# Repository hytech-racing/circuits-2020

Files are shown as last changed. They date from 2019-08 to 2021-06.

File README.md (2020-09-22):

HyTech Logo

# 2020 Circuits

Repository for all of the circuits for the 2019-2020 car.

## Getting Started with this Git Repository
1. Follow HyTech's [Software Guide](https://github.com/hytech-racing/training/tree/master/Resources).
2. Create a GitHub account if you don't already have one.
3. Download and install [GitHub Desktop](https://desktop.github.com/) (basic) or [Git CLI](https://git-scm.com/book/en/v2/Getting-Started-Installing-Git) (advanced).
    * If you are using GitHub Desktop for the first time, be sure to read the [User Guide](https://help.github.com/desktop/guides/).
    * If you are using Git for the first time, you should start off by reading a tutorial. There are many available online:
        * [Pro Git book](https://git-scm.com/book/en/v2)
        * [Atlassian Git Tutorial](https://www.atlassian.com/git/tutorials/)
    * You may want to keep a copy of [GitHub's Git Cheat Sheet](https://services.github.com/kit/downloads/github-git-cheat-sheet.pdf) as a reference.
4. Talk to your subteam lead to be added to the team within the GitHub organization.
5. Clone this repository to your computer using the URLs:
    * SSH: `git@github.com:hytech-racing/circuits-2020.git`
    * HTTPS: `https://github.com/hytech-racing/circuits-2020.git`

## Getting Started with EAGLE
1. Follow HyTech's [Software Guide](https://github.com/hytech-racing/training/tree/master/Resources).
2. Download and install [EAGLE](https://www.autodesk.com/products/eagle/overview)
3. Get the free [Educational License](https://www.autodesk.com/education/free-software/eagle) (a .edu email address is required)

## Circuit Board Versioning Scheme
* New boards must start their numbering at revision 1.
* Revision numbers must be incremented by 1 when a physical board is manufactured, but not at any other time.
* After a board is manufactured, the files corresponding to the manufactured version should not be modified.
* Circuit boards based off of a previous year's design should increment based off of the previous board's revision number.

## More Information
* [Software Guide](https://github.com/hytech-racing/training/tree/master/Resources)
* [Team Site](https://hytechracing.gatech.edu/)
* [Facebook](https://www.facebook.com/HyTechRacing/)
* [Engage](https://gatech.campuslabs.com/engage/organization/hytech-racing)

## License
This project is licensed under the GPL License v3.0. See the [LICENSE](LICENSE) file for more information.

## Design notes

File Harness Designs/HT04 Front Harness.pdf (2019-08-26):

QA

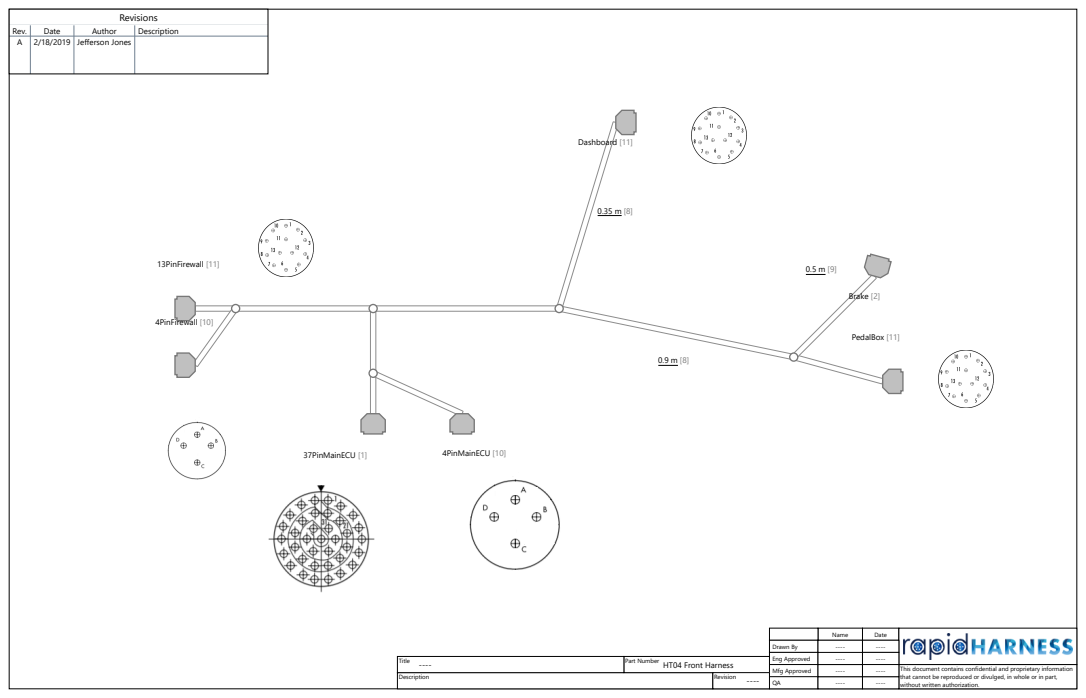
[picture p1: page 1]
Description; Mfg Approved; Part Number; Revision; Revisions; Brake [2]; Dashboard [11]; 4PinFirewall [10]; 13PinFirewall [11]; 37PinMainECU [1] 4PinMainECU [10]; PedalBox [11]

Rev. Date Author Description
A 2/18/2019 Jefferson Jones
Title HT04 Front Harness

Name Date
Drawn By
Eng Approved
This document contains confidential and proprietary information
that cannot be reproduced or divulged, in whole or in part,
without written authorization.

Id Type Manufacturer Part Number Description Quantity Usage

### 1 Connector TE:Deutsch AS614-35PN 37 Pin Plug, 22 Gauge 1 37PinMainECU

### 2 Connector 3 Cavity Generic Connector 1 Brake

3 Wire 22 AWG Red Generic Wire ≥ 3.55 m ACCEL1_5V, ACCEL2_5V,
BRAKE_5V, BrakeLight,
DASH12V, InverterSupply, SSOK
4 Wire 22 AWG White Generic Wire ≥ 4.2 m DASH1, DASH2, DASH3, DASH4,
DASH5, DASH6, DASH7, DASH8, DASH9, DASH10, DASH11, DASH12
5 Wire 22 AWG Green Generic Wire ≥ 3.2 m ACCEL1_GND, ACCEL2_GND,
BRAKE_GND
6 Wire 22 AWG Yellow Generic Wire ≥ 3.2 m ACCEL1, ACCEL2, BMSOK, BRAKE,
LatchEXTButton, OKHS, W4, W5
7 Wire 16 AWG Violet Generic Wire ≥ 2.5 m SHUTDOWN_D, SHUTDOWN_E,
SHUTDOWN_F, W1

### 8 Tubing Raychem 1/2" Raychem 1/2" 1.25 m See Drawing

### 9 Tubing Raychem 1/4" Raychem 1/4" 0.5 m See Drawing

### 10 Connector TE:Deutsch AS612-04SN 4 Pin Plug, 16 Gauge 2 4PinFirewall, 4PinMainECU

11 Connector TE:Deutsch AS610-35PN Plug 13 Pin Autosport Connector 3 13PinFirewall, Dashboard,
PedalBox

### 12 Wire 16 AWG Green Generic Wire Fan1GND, GND, PumpGND

### 13 Wire 16 AWG Red Generic Wire 12VIN, Fan1

### 14 Cable CAN Cable Cable for CAN Communications and Power CBL1

### 15 Wire 22 AWG Black Generic Wire ≥ 0.35 m DASHGND, GNDShield

### Bill of Materials 1 of 1 Page 2 of 6

Part Number:

Title:

Description:

HT04 Front Harness

### From To Conductor Conductor PN Twisted With Gauge Length From Contact PN Notes

4PinFirewall.1 4PinMainECU.1 12VIN.Red 16 AWG Red 16 AWG
4PinFirewall.2 4PinMainECU.2 PumpGND.Green 16 AWG Green 16 AWG
4PinFirewall.3 4PinMainECU.3 Fan1GND.Green 16 AWG Green 16 AWG
4PinFirewall.4 4PinMainECU.4 GND.Green 16 AWG Green 16 AWG 13PinFirewall.12 Dashboard.13 SHUTDOWN_F.Violet 16 AWG Violet 16 AWG ≥ 0.35 m 13PinFirewall.13 Dashboard.16 SSOK.Red 22 AWG Red 22 AWG ≥ 0.35 m 37PinMainECU.1 Dashboard.2 DASH1.White 22 AWG White 22 AWG ≥ 0.35 m 37PinMainECU.2 Dashboard.3 DASH2.White 22 AWG White 22 AWG ≥ 0.35 m 37PinMainECU.3 Dashboard.4 DASH3.White 22 AWG White 22 AWG ≥ 0.35 m 37PinMainECU.4 Dashboard.5 DASH4.White 22 AWG White 22 AWG ≥ 0.35 m 37PinMainECU.5 PedalBox.12 SHUTDOWN_D.Violet 16 AWG Violet 16 AWG ≥ 0.9 m 37PinMainECU.6 Dashboard.12 DASH11.White 22 AWG White 22 AWG ≥ 0.35 m 37PinMainECU.7 13PinFirewall.2 InverterSupply.Red 22 AWG Red 22 AWG 37PinMainECU.8 Brake.3 BRAKE.Yellow 22 AWG Yellow 22 AWG ≥ 1.4 m 37PinMainECU.9 13PinFirewall.3 BrakeLight.Red 22 AWG Red 22 AWG 37PinMainECU.10 13PinFirewall.4 CBL1.Red-PWR CAN Cable 22 AWG 37PinMainECU.11 13PinFirewall.5 CBL1.White-CANL CAN Cable 22 AWG 37PinMainECU.12 13PinFirewall.6 CBL1.Green-CANH CAN Cable 22 AWG 37PinMainECU.14 Brake.2 BRAKE_GND.Green 22 AWG Green 22 AWG ≥ 1.4 m 37PinMainECU.15 PedalBox.1 ACCEL2_GND.Green 22 AWG Green 22 AWG ≥ 0.9 m 37PinMainECU.16 PedalBox.5 ACCEL1_GND.Green 22 AWG Green 22 AWG ≥ 0.9 m 37PinMainECU.17 13PinFirewall.7 Fan1.Red 16 AWG Red 16 AWG 37PinMainECU.18 Dashboard.6 DASH5.White 22 AWG White 22 AWG ≥ 0.35 m 37PinMainECU.19 Dashboard.7 DASH6.White 22 AWG White 22 AWG ≥ 0.35 m 37PinMainECU.20 Dashboard.8 DASH7.White 22 AWG White 22 AWG ≥ 0.35 m 37PinMainECU.21 Dashboard.9 DASH8.White 22 AWG White 22 AWG ≥ 0.35 m 37PinMainECU.22 Dashboard.13 DASH12.White 22 AWG White 22 AWG ≥ 0.35 m 37PinMainECU.23 Dashboard.10 DASH9.White 22 AWG White 22 AWG ≥ 0.35 m 37PinMainECU.24 PedalBox.4 ACCEL2.Yellow 22 AWG Yellow 22 AWG ≥ 0.9 m 37PinMainECU.25 PedalBox.3 ACCEL1.Yellow 22 AWG Yellow 22 AWG ≥ 0.9 m 37PinMainECU.27 PedalBox.6 ACCEL1_5V.Red 22 AWG Red 22 AWG ≥ 0.9 m 37PinMainECU.28 PedalBox.2 ACCEL2_5V.Red 22 AWG Red 22 AWG ≥ 0.9 m 37PinMainECU.29 Brake.1 BRAKE_5V.Red 22 AWG Red 22 AWG ≥ 1.4 m 37PinMainECU.30 13PinFirewall.8 CBL1.Black-GND CAN Cable 22 AWG 37PinMainECU.31 13PinFirewall.9 BMSOK.Yellow 22 AWG Yellow 22 AWG 37PinMainECU.32 Dashboard.11 DASH10.White 22 AWG White 22 AWG ≥ 0.35 m 37PinMainECU.33 13PinFirewall.10 OKHS.Yellow 22 AWG Yellow 22 AWG 37PinMainECU.36 13PinFirewall.1 GNDShield.Black 22 AWG Black 22 AWG 37PinMainECU.36 Dashboard.1 DASHGND.Black 22 AWG Black 22 AWG ≥ 0.35 m
37PinMainECU.37 13PinFirewall.11 LatchEXTButton.Yellow 22 AWG Yellow 22 AWG
Dashboard.12 PedalBox.13 SHUTDOWN_E.Violet 16 AWG Violet 16 AWG ≥ 1.25 m

### Wiring Table 1 of 1 Page 3 of 6

Description:

### # Type Reference Designator Manufacturer Part Number Color Gauge Length Twisted With

### 1 Cable CBL1 CAN Cable Gray

### 2 Wire 12VIN 16 AWG Red Red 16 AWG

### 3 Wire ACCEL1 22 AWG Yellow Yellow 22 AWG ≥ 0.9 m 4 Wire ACCEL1_5V 22 AWG Red Red 22 AWG ≥ 0.9 m

### 5 Wire ACCEL1_GND 22 AWG Green Green 22 AWG ≥ 0.9 m

### 6 Wire ACCEL2 22 AWG Yellow Yellow 22 AWG ≥ 0.9 m 7 Wire ACCEL2_5V 22 AWG Red Red 22 AWG ≥ 0.9 m

### 8 Wire ACCEL2_GND 22 AWG Green Green 22 AWG ≥ 0.9 m

### 9 Wire BMSOK 22 AWG Yellow Yellow 22 AWG

### 10 Wire BRAKE 22 AWG Yellow Yellow 22 AWG ≥ 1.4 m 11 Wire BRAKE_5V 22 AWG Red Red 22 AWG ≥ 1.4 m

### 12 Wire BRAKE_GND 22 AWG Green Green 22 AWG ≥ 1.4 m

### 13 Wire BrakeLight 22 AWG Red Red 22 AWG

14 Wire DASH1 22 AWG White White 22 AWG ≥ 0.35 m 15 Wire DASH2 22 AWG White White 22 AWG ≥ 0.35 m 16 Wire DASH3 22 AWG White White 22 AWG ≥ 0.35 m 17 Wire DASH4 22 AWG White White 22 AWG ≥ 0.35 m 18 Wire DASH5 22 AWG White White 22 AWG ≥ 0.35 m 19 Wire DASH6 22 AWG White White 22 AWG ≥ 0.35 m 20 Wire DASH7 22 AWG White White 22 AWG ≥ 0.35 m 21 Wire DASH8 22 AWG White White 22 AWG ≥ 0.35 m 22 Wire DASH9 22 AWG White White 22 AWG ≥ 0.35 m 23 Wire DASH10 22 AWG White White 22 AWG ≥ 0.35 m 24 Wire DASH11 22 AWG White White 22 AWG ≥ 0.35 m 25 Wire DASH12 22 AWG White White 22 AWG ≥ 0.35 m

### 26 Wire DASH12V 22 AWG Red Red 22 AWG 0 in

### 27 Wire DASHGND 22 AWG Black Black 22 AWG ≥ 0.35 m

### 28 Wire Fan1 16 AWG Red Red 16 AWG

### 29 Wire Fan1GND 16 AWG Green Green 16 AWG 30 Wire GND 16 AWG Green Green 16 AWG

### 31 Wire GNDShield 22 AWG Black Black 22 AWG

### 32 Wire InverterSupply 22 AWG Red Red 22 AWG

### 33 Wire LatchEXTButton 22 AWG Yellow Yellow 22 AWG 34 Wire OKHS 22 AWG Yellow Yellow 22 AWG

### 35 Wire PumpGND 16 AWG Green Green 16 AWG

### 36 Wire SHUTDOWN_D 16 AWG Violet Violet 16 AWG ≥ 0.9 m

### 37 Wire SHUTDOWN_E 16 AWG Violet Violet 16 AWG ≥ 1.25 m 38 Wire SHUTDOWN_F 16 AWG Violet Violet 16 AWG ≥ 0.35 m

### 39 Wire SSOK 22 AWG Red Red 22 AWG ≥ 0.35 m

### 40 Wire W1 16 AWG Violet Violet 16 AWG 0 in 41 Wire W4 22 AWG Yellow Yellow 22 AWG 0 in

### Cutlist 1 of 2 Page 4 of 6

Description:

### # Type Reference Designator Manufacturer Part Number Color Gauge Length Twisted With

### 42 Wire W5 22 AWG Yellow Yellow 22 AWG 0 in

### Cutlist 2 of 2 Page 5 of 6

Description:

# Manufacturer Part Number Description Label Text

### Labels 1 of 1 Page 6 of 6

Description:

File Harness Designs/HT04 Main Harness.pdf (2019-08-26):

QA

1

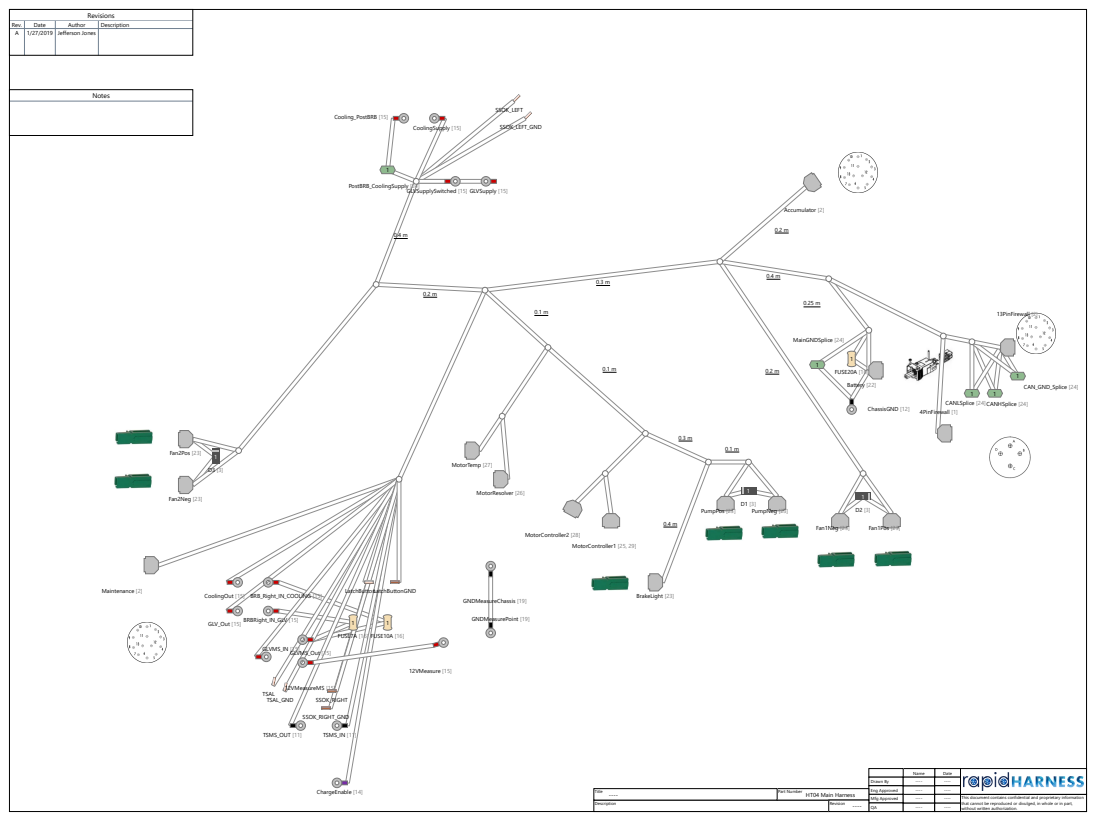
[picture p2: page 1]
Description; Mfg Approved; Part Number; Revision; Title HT04 Main Harness; Notes; Revisions; Accumulator [2]; Battery [22]; MotorController1 [25, 29]; Fan1Neg [23] Fan1Pos [23]; Fan2Pos [23] Fan2Neg [23]; PumpPos [23] PumpNeg [23]; BrakeLight [23]; 13PinFirewall [2]; 4PinFirewall [1]; Maintenance [2]; MotorResolver [26]; MotorTemp [27]; MotorController2 [28]; SSOK_RIGHT; TSAL; LatchButton; SSOK_LEFT; LatchButtonGND; TSAL_GND; SSOK_RIGHT_GND; SSOK_LEFT_GND; TSMS_IN [11]; ChassisGND [12]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

Rev. Date Author Description
A 1/27/2019 Jefferson Jones

Name Date
Drawn By
Eng Approved
This document contains confidential and proprietary information
that cannot be reproduced or divulged, in whole or in part,
without written authorization.

Id Type Manufacturer Part Number Description Quantity Usage

### 1 Connector TE:Deutsch AS612-04SN 4 Pin Plug, 16 Gauge 1 4PinFirewall

2 Connector TE AS610-35PN Plug 13 Pin Autosport Connector 3 13PinFirewall, Accumulator,
Maintenance

### 3 Diode Generic Diode Generic Diode 3 D1, D2, D3

4 Wire 16 AWG Red Generic Wire ≥ 8.65 m 12VBattery_toFuse,
12VMeasureCable,
12V_IntoMainECU,
BatteryFuse_toGLVMS,
CoolingPWR,
Cooling_RightBRB_toLeftBRB, Cooling_toRightBRB, Fan1PWR,
Fan2PWR,
GLV_RightBRB_toLeftBRB,
GLV_ToCoolingFuse,
GLV_ToECUFuse,
LVFused_toRightBRB, PumpPWR,
SSOKL, SSOKR, TSALPWR

### 5 Wire 16 AWG Brown Generic Wire 0 in W10, W11, W12, W13, W14, W15

6 Wire 22 AWG White Generic Wire ≥ 1.5 m DASH12,
MCMaintFaultIndication,
MCMaintRX, MCMaintTX,
MCMaintXDCR_PWR, MotorCosNeg,
MotorCosPos, MotorExcNeg,
MotorExcPos, MotorSinNeg,
MotorSinPos, MotorTempNeg
7 Wire 22 AWG Red Generic Wire ≥ 1.6 m BrakeLightPWR, BrakePWR,
DASH12V, PedalPWR1, PedalPWR2

### 8 Wire 22 AWG Brown Generic Wire 0 in W29, W30, W31

9 Wire 22 AWG Yellow Generic Wire ≥ 2.2 m BMSOK, BrakeSignal,
LatchButtonSignal,
MCMaintProgEnable,
MotorTempPos, OKHS
10 Wire 16 AWG Violet Generic Wire ≥ 1.7 m ChargeEnableSignal,
MaintChargeEnable,
SHUTDOWN_F, SHUTDOWN_G

### 11 Ring Terminal Unspecified gauge Black Generic Ring Terminal 2 TSMS_IN, TSMS_OUT

### 12 Ring Terminal 14-12 AWG Black Generic Ring Terminal 1 ChassisGND

13 Cable CAN Cable Cable for CAN Communications and Power ≥ 2.2 m AccumCAN, CANMaint,
MotorController_CAN

### 14 Ring Terminal Unspecified gauge Violet Generic Ring Terminal 1 ChargeEnable

15 Ring Terminal Unspecified gauge Red Generic Ring Terminal 12 12VMeasure, 12VMeasureMS,

### Bill of Materials 1 of 2 Page 2 of 9

Part Number:

Title:

Description:

HT04 Main Harness

Id Type Manufacturer Part Number Description Quantity Usage
BRBRight_IN_GLV,
BRB_Right_IN_COOLING,
CoolingOut, CoolingSupply, Cooling_PostBRB, GLVMS_IN,
GLVMS_Out, GLVSupply,
GLVSupplySwitched, GLV_Out

### 16 Resistor Generic Resistor Generic Resistor 3 FUSE7A, FUSE10A, FUSE20A

17 Wire 16 AWG Green Generic Wire ≥ 6.5 m Fan1GND, Fan2GND,
GLVBattery_ChassisGND,
GNDMeasure, MainECUGND,
PumpGND, SSOKL_GND,
SSOKR_GND, TSALGND, W65

### 18 Wire 22 AWG Black Generic Wire ≥ 0.2 m MCMaintGND

19 Ring Terminal 26-22 AWG Black Generic Ring Terminal 2 GNDMeasureChassis,
GNDMeasurePoint
20 Wire 22 AWG Green Generic Wire ≥ 2.8 m Accel1GND, Accel2GND,
BrakeGND,
BrakeLightGNDConnection,
LatchGND, W70

### 21 Wire 16 AWG Black Generic Wire MainGNDSpliceToGND

### 22 Connector ASMPP30-1X2-RK Anderson PowerPole 1X2 1 Battery

23 Connector 1327G6-BK Anderson PowerPole 1 7 BrakeLight, Fan1Neg, Fan1Pos,
Fan2Neg, Fan2Pos, PumpNeg,
PumpPos
24 Splice Generic Splice Generic Splice 5 CANHSplice, CANLSplice,
CAN_GND_Splice,
MainGNDSplice,
PostBRB_CoolingSupply

### 25 Boot TE 776463/776464 Ampseal Boot 1 MotorController1

### 26 Connector 8STA60835SN 1 MotorResolver

### 27 Connector 8STA60235SN 1 MotorTemp

### 28 Connector 8 Cavity Generic Connector 1 MotorController2

### 29 Connector 12 Cavity Generic Connector 1 MotorController1

### Bill of Materials 2 of 2 Page 3 of 9

Description:

From To Conductor Conductor PN Twisted With Gauge Length From Contact PN Notes
12VMeasure 12VMeasureMS 12VMeasureCable.Red 16 AWG Red 16 AWG
13PinFirewall.1 MainGNDSplice ≥ 0.25 m ShieldGND 13PinFirewall.5 CANLSplice CANL fromFirewall 13PinFirewall.6 CANHSplice CANH from Firewall
13PinFirewall.8 CAN_GND_Splice
Accumulator.2 ChargeEnable ChargeEnableSignal.Violet 16 AWG Violet 16 AWG ≥ 0.5 m ChargeEnable Signal Accumulator.4 13PinFirewall.9 BMSOK.Yellow 22 AWG Yellow 22 AWG ≥ 0.6 m BMS_OK Accumulator.5 13PinFirewall.10 OKHS.Yellow 22 AWG Yellow 22 AWG ≥ 0.6 m OKHS Accumulator.7 13PinFirewall.4 AccumCAN.Red-PWR CAN Cable 22 AWG ≥ 0.6 m 12V for Accumulator Accumulator.8 CAN_GND_Splice AccumCAN.Black-GND CAN Cable 22 AWG ≥ 0.6 m GND for Accumulator Accumulator.9 CANLSplice AccumCAN.White-CANL CAN Cable 22 AWG ≥ 0.6 m CANL For Accumulator Accumulator.10 CANHSplice AccumCAN.Green-CANH CAN Cable 22 AWG ≥ 0.6 m Accumulator CANH
BRBRight_IN_GLV FUSE7A.NEG LVFused_toRightBRB.Red 16 AWG Red 16 AWG
BRB_Right_IN_COOLING FUSE10A.NEG Cooling_toRightBRB.Red 16 AWG Red 16 AWG
Battery.2 4PinFirewall.4 MainECUGND.Green 16 AWG Green 16 AWG ≥ 0.25 m MainGND BrakeLight.1 13PinFirewall.3 BrakeLightPWR.Red 22 AWG Red 22 AWG ≥ 1.6 m Brake Light PWR
ChassisGND Battery.2 GLVBattery_ChassisGND.Green 16 AWG Green 16 AWG
CoolingOut CoolingSupply Cooling_RightBRB_toLeftBRB.Red 16 AWG Red 16 AWG ≥ 0.6 m Cooling Supply before second BRB
Cooling_PostBRB PostBRB_CoolingSupply CoolingPWR.Red 16 AWG Red 16 AWG
FUSE20A.NEG GLVMS_IN BatteryFuse_toGLVMS.Red 16 AWG Red 16 AWG ≥ 0.95 m Battery+ Fused FUSE20A.POS Battery.1 12VBattery_toFuse.Red 16 AWG Red 16 AWG Battery+ Unfused Fan1Neg.1 13PinFirewall.7 Fan1GND.Green 16 AWG Green 16 AWG ≥ 0.6 m Fan1-
Fan1Neg.1 D2.NEG
Fan1Pos.1 D2.POS
Fan1Pos.1 PostBRB_CoolingSupply Fan1PWR.Red 16 AWG Red 16 AWG ≥ 1.1 m Power for Fan1 Fan2Neg.1 4PinFirewall.3 Fan2GND.Green 16 AWG Green 16 AWG ≥ 0.9 m Fan2-
Fan2Neg.1 D3.NEG
Fan2Pos.1 D3.POS
Fan2Pos.1 PostBRB_CoolingSupply Fan2PWR.Red 16 AWG Red 16 AWG ≥ 0.4 m Power for Fan2
GLVMS_Out FUSE7A.POS GLV_ToECUFuse.Red 16 AWG Red 16 AWG
GLVMS_Out FUSE10A.POS GLV_ToCoolingFuse.Red 16 AWG Red 16 AWG
GLVSupplySwitched 4PinFirewall.1 12V_IntoMainECU.Red 16 AWG Red 16 AWG ≥ 1.3 m Power for GLV System
GLV_Out GLVSupply GLV_RightBRB_toLeftBRB.Red 16 AWG Red 16 AWG ≥ 0.6 m
GNDMeasureChassis GNDMeasurePoint GNDMeasure.Green 16 AWG Green 16 AWG
LatchButton 13PinFirewall.11 LatchButtonSignal.Yellow 22 AWG Yellow 22 AWG ≥ 0.7 m
LatchButtonGND MainGNDSplice LatchGND.Green 22 AWG Green 22 AWG ≥ 0.95 m MainGNDSplice BrakeLight.NegLead BrakeLightGNDConnection.Green 22 AWG Green 22 AWG ≥ 1.85 m
MainGNDSplice ChassisGND MainGNDSpliceToGND.Black 16 AWG Black 16 AWG GND
MainGNDSplice SSOK_LEFT_GND SSOKL_GND.Green 16 AWG Green 16 AWG ≥ 1.55 m MainGNDSplice SSOK_RIGHT_GND SSOKR_GND.Green 16 AWG Green 16 AWG ≥ 0.95 m MainGNDSplice TSAL_GND TSALGND.Green 16 AWG Green 16 AWG ≥ 0.95 m

### Wiring Table 1 of 2 Page 4 of 9

Description:

From To Conductor Conductor PN Twisted With Gauge Length From Contact PN Notes
Maintenance.3 MotorController1.7 MCMaintGND.Black 22 AWG Black 22 AWG ≥ 0.2 m
Maintenance.4 MotorController1.8 MCMaintProgEnable.Yellow 22 AWG Yellow 22 AWG ≥ 0.2 m
Maintenance.5 MotorController1.9 MCMaintXDCR_PWR.White 22 AWG White 22 AWG ≥ 0.2 m
Maintenance.6 MotorController1.10 MCMaintFaultIndication.White 22 AWG White 22 AWG ≥ 0.2 m Maintenance.8 13PinFirewall.8 CANMaint.Black-GND CAN Cable 22 AWG ≥ 0.7 m Maintenance.9 CANLSplice CANMaint.White-CANL CAN Cable 22 AWG ≥ 0.7 m
Maintenance.10 CANLSplice CANMaint.Green-CANH CAN Cable 22 AWG ≥ 0.7 m
Maintenance.11 ChargeEnable MaintChargeEnable.Violet 16 AWG Violet 16 AWG
MotorController1.1 13PinFirewall.2 MotorController_CAN.Red-PWR CAN Cable 22 AWG ≥ 0.9 m Motor Controller PWR MotorController1.2 CAN_GND_Splice MotorController_CAN.Black-GND CAN Cable 22 AWG ≥ 0.9 m Motor Controller GND MotorController1.3 CANHSplice MotorController_CAN.Green-CANH CAN Cable 22 AWG ≥ 0.9 m Motor Controller CANH MotorController1.4 CANLSplice MotorController_CAN.White-CANL CAN Cable 22 AWG ≥ 0.9 m Motor Controller CANL
MotorController1.5 Maintenance.1 MCMaintTX.White 22 AWG White 22 AWG ≥ 0.2 m
MotorController1.6 Maintenance.2 MCMaintRX.White 22 AWG White 22 AWG ≥ 0.2 m
MotorController2.2 MotorResolver.1 MotorExcPos.White 22 AWG White 22 AWG ≥ 0.1 m
MotorController2.3 MotorResolver.2 MotorExcNeg.White 22 AWG White 22 AWG ≥ 0.1 m MotorController2.4 MotorResolver.3 MotorSinPos.White 22 AWG White 22 AWG ≥ 0.1 m MotorController2.5 MotorResolver.4 MotorSinNeg.White 22 AWG White 22 AWG ≥ 0.1 m MotorController2.6 MotorResolver.5 MotorCosPos.White 22 AWG White 22 AWG ≥ 0.1 m MotorController2.7 MotorResolver.6 MotorCosNeg.White 22 AWG White 22 AWG ≥ 0.1 m MotorController2.8 MotorTemp.2 MotorTempNeg.White 22 AWG White 22 AWG ≥ 0.1 m
MotorTemp.1 MotorController2.1 MotorTempPos.Yellow 22 AWG Yellow 22 AWG ≥ 0.1 m
PumpNeg.1 4PinFirewall.2 PumpGND.Green 16 AWG Green 16 AWG ≥ 1.3 m Pump1-
PumpNeg.1 D1.NEG
PumpPos.1 D1.POS
PumpPos.1 PostBRB_CoolingSupply PumpPWR.Red 16 AWG Red 16 AWG ≥ 1.2 m Power for Pump SSOK_LEFT 13PinFirewall.13 SSOKL.Red 16 AWG Red 16 AWG ≥ 1.3 m SSOK+Left Panel SSOK_RIGHT 13PinFirewall.13 SSOKR.Red 16 AWG Red 16 AWG ≥ 0.7 m SSOK Supply TSAL Accumulator.1 TSALPWR.Red 16 AWG Red 16 AWG ≥ 0.5 m TSAL TSMS_IN 13PinFirewall.12 SHUTDOWN_F.Violet 16 AWG Violet 16 AWG ≥ 0.7 m SHUTDOWN TSMS_OUT Accumulator.6 SHUTDOWN_G.Violet 16 AWG Violet 16 AWG ≥ 0.5 m SHUTDOWN6

### Wiring Table 2 of 2 Page 5 of 9

Description:

# Type Reference Designator Manufacturer Part Number Color Gauge Length Twisted With

### 1 Cable AccumCAN CAN Cable Gray ≥ 0.6 m 2 Cable CANMaint CAN Cable Gray ≥ 0.7 m 3 Cable MotorController_CAN CAN Cable Gray ≥ 0.9 m

### 4 Wire 12VBattery_toFuse 16 AWG Red Red 16 AWG 5 Wire 12VMeasureCable 16 AWG Red Red 16 AWG

### 6 Wire 12V_IntoMainECU 16 AWG Red Red 16 AWG ≥ 1.3 m

### 7 Wire Accel1GND 22 AWG Green Green 22 AWG 0 in 8 Wire Accel2GND 22 AWG Green Green 22 AWG 0 in

### 9 Wire BMSOK 22 AWG Yellow Yellow 22 AWG ≥ 0.6 m

### 10 Wire BatteryFuse_toGLVMS 16 AWG Red Red 16 AWG ≥ 0.95 m

### 11 Wire BrakeGND 22 AWG Green Green 22 AWG 0 in

### 12 Wire BrakeLightGNDConnection 22 AWG Green Green 22 AWG ≥ 1.85 m

### 13 Wire BrakeLightPWR 22 AWG Red Red 22 AWG ≥ 1.6 m

### 14 Wire BrakePWR 22 AWG Red Red 22 AWG 0 in

### 15 Wire BrakeSignal 22 AWG Yellow Yellow 22 AWG 0 in

### 16 Wire ChargeEnableSignal 16 AWG Violet Violet 16 AWG ≥ 0.5 m

### 17 Wire CoolingPWR 16 AWG Red Red 16 AWG

### 18 Wire Cooling_RightBRB_toLeftBRB 16 AWG Red Red 16 AWG ≥ 0.6 m

### 19 Wire Cooling_toRightBRB 16 AWG Red Red 16 AWG

### 20 Wire DASH12 22 AWG White White 22 AWG 0 in

### 21 Wire DASH12V 22 AWG Red Red 22 AWG 0 in

### 22 Wire Fan1GND 16 AWG Green Green 16 AWG ≥ 0.6 m

### 23 Wire Fan1PWR 16 AWG Red Red 16 AWG ≥ 1.1 m

### 24 Wire Fan2GND 16 AWG Green Green 16 AWG ≥ 0.9 m

### 25 Wire Fan2PWR 16 AWG Red Red 16 AWG ≥ 0.4 m

### 26 Wire GLVBattery_ChassisGND 16 AWG Green Green 16 AWG

### 27 Wire GLV_RightBRB_toLeftBRB 16 AWG Red Red 16 AWG ≥ 0.6 m

### 28 Wire GLV_ToCoolingFuse 16 AWG Red Red 16 AWG 29 Wire GLV_ToECUFuse 16 AWG Red Red 16 AWG

### 30 Wire GNDMeasure 16 AWG Green Green 16 AWG

### 31 Wire LVFused_toRightBRB 16 AWG Red Red 16 AWG

### 32 Wire LatchButtonSignal 22 AWG Yellow Yellow 22 AWG ≥ 0.7 m

### 33 Wire LatchGND 22 AWG Green Green 22 AWG ≥ 0.95 m

### 34 Wire MCMaintFaultIndication 22 AWG White White 22 AWG ≥ 0.2 m 35 Wire MCMaintGND 22 AWG Black Black 22 AWG ≥ 0.2 m

### 36 Wire MCMaintProgEnable 22 AWG Yellow Yellow 22 AWG ≥ 0.2 m

### 37 Wire MCMaintRX 22 AWG White White 22 AWG ≥ 0.2 m 38 Wire MCMaintTX 22 AWG White White 22 AWG ≥ 0.2 m 39 Wire MCMaintXDCR_PWR 22 AWG White White 22 AWG ≥ 0.2 m

### 40 Wire MainECUGND 16 AWG Green Green 16 AWG ≥ 0.25 m

### 41 Wire MainGNDSpliceToGND 16 AWG Black Black 16 AWG

### Cutlist 1 of 3 Page 6 of 9

Description:

# Type Reference Designator Manufacturer Part Number Color Gauge Length Twisted With

### 42 Wire MaintChargeEnable 16 AWG Violet Violet 16 AWG

43 Wire MotorCosNeg 22 AWG White White 22 AWG ≥ 0.1 m 44 Wire MotorCosPos 22 AWG White White 22 AWG ≥ 0.1 m 45 Wire MotorExcNeg 22 AWG White White 22 AWG ≥ 0.1 m 46 Wire MotorExcPos 22 AWG White White 22 AWG ≥ 0.1 m 47 Wire MotorSinNeg 22 AWG White White 22 AWG ≥ 0.1 m 48 Wire MotorSinPos 22 AWG White White 22 AWG ≥ 0.1 m 49 Wire MotorTempNeg 22 AWG White White 22 AWG ≥ 0.1 m

### 50 Wire MotorTempPos 22 AWG Yellow Yellow 22 AWG ≥ 0.1 m 51 Wire OKHS 22 AWG Yellow Yellow 22 AWG ≥ 0.6 m

### 52 Wire PedalPWR1 22 AWG Red Red 22 AWG 0 in 53 Wire PedalPWR2 22 AWG Red Red 22 AWG 0 in

### 54 Wire PumpGND 16 AWG Green Green 16 AWG ≥ 1.3 m

### 55 Wire PumpPWR 16 AWG Red Red 16 AWG ≥ 1.2 m 56 Wire SHUTDOWN_F 16 AWG Violet Violet 16 AWG ≥ 0.7 m 57 Wire SHUTDOWN_G 16 AWG Violet Violet 16 AWG ≥ 0.5 m 58 Wire SSOKL 16 AWG Red Red 16 AWG ≥ 1.3 m

### 59 Wire SSOKL_GND 16 AWG Green Green 16 AWG ≥ 1.55 m

### 60 Wire SSOKR 16 AWG Red Red 16 AWG ≥ 0.7 m

### 61 Wire SSOKR_GND 16 AWG Green Green 16 AWG ≥ 0.95 m 62 Wire TSALGND 16 AWG Green Green 16 AWG ≥ 0.95 m

### 63 Wire TSALPWR 16 AWG Red Red 16 AWG ≥ 0.5 m

64 Wire W10 16 AWG Brown Brown 16 AWG 0 in 65 Wire W11 16 AWG Brown Brown 16 AWG 0 in 66 Wire W12 16 AWG Brown Brown 16 AWG 0 in 67 Wire W13 16 AWG Brown Brown 16 AWG 0 in 68 Wire W14 16 AWG Brown Brown 16 AWG 0 in 69 Wire W15 16 AWG Brown Brown 16 AWG 0 in 70 Wire W29 22 AWG Brown Brown 22 AWG 0 in 71 Wire W30 22 AWG Brown Brown 22 AWG 0 in 72 Wire W31 22 AWG Brown Brown 22 AWG 0 in

### 73 Wire W65 16 AWG Green Green 16 AWG 0 in 74 Wire W70 22 AWG Green Green 22 AWG 0 in

75 13PinFirewall.1 - MainGNDSplice ≥ 0.25 m
76 13PinFirewall.5 - CANLSplice
77 13PinFirewall.6 - CANHSplice
78 13PinFirewall.8 - CAN_GND_Splice

### 79 Fan1Neg.1 - D2.NEG

### 80 Fan1Pos.1 - D2.POS

### 81 Fan2Neg.1 - D3.NEG

### 82 Fan2Pos.1 - D3.POS

### Cutlist 2 of 3 Page 7 of 9

Description:

# Type Reference Designator Manufacturer Part Number Color Gauge Length Twisted With

### 83 PumpNeg.1 - D1.NEG

### 84 PumpPos.1 - D1.POS

### Cutlist 3 of 3 Page 8 of 9

Description:

# Manufacturer Part Number Description Label Text

### Labels 1 of 1 Page 9 of 9

Description:

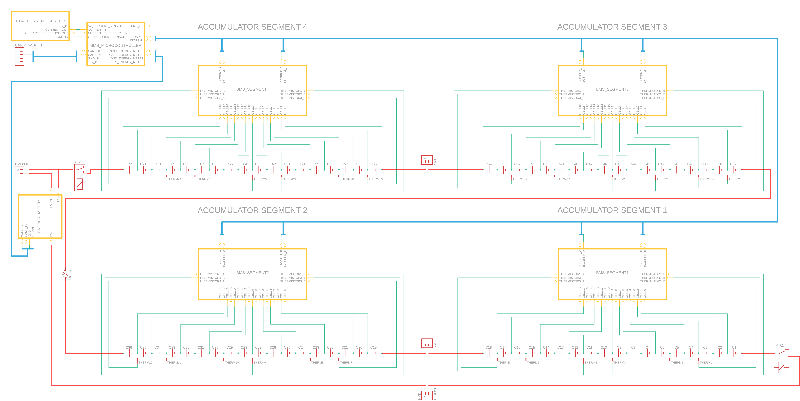
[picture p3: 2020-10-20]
EAGLE Board Designs/BMS/BMS System Layout Schematic/BMS Layout rev6.png

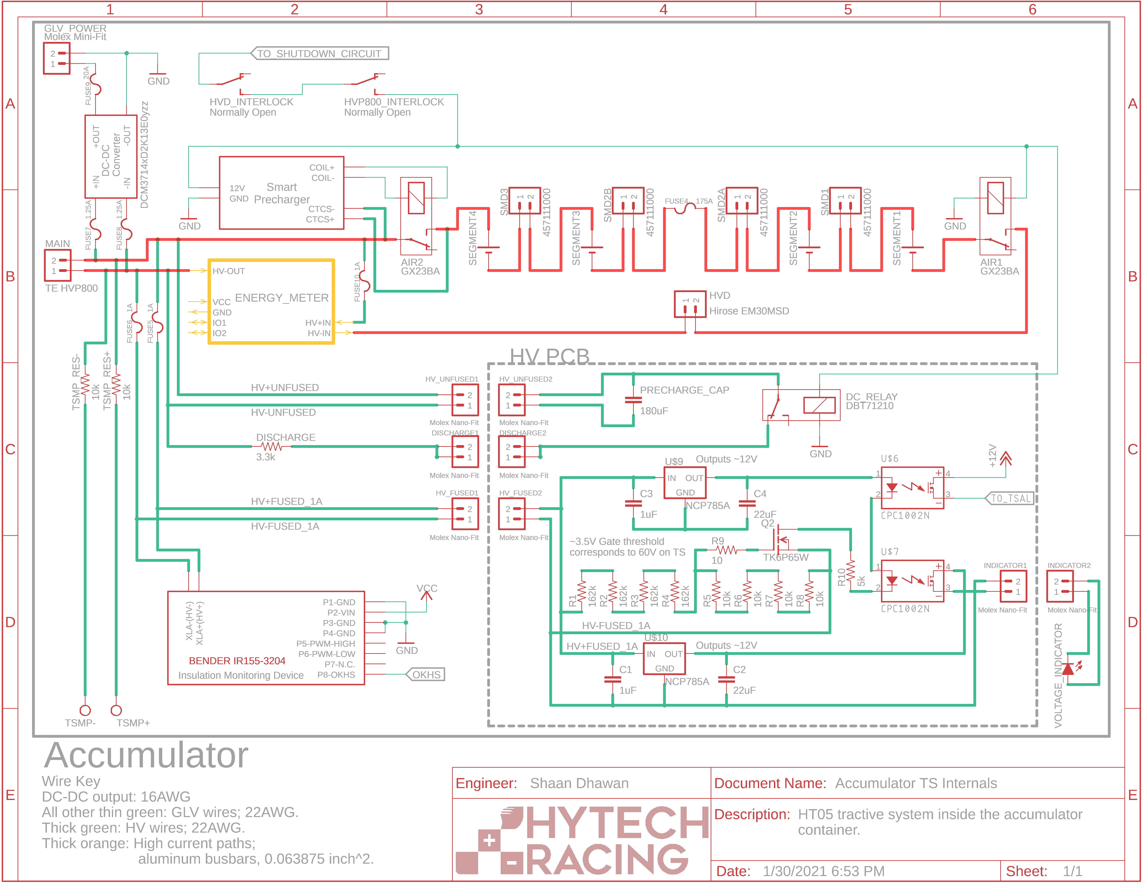
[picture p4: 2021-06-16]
ESF Schematics/Accumulator TS Internals.png

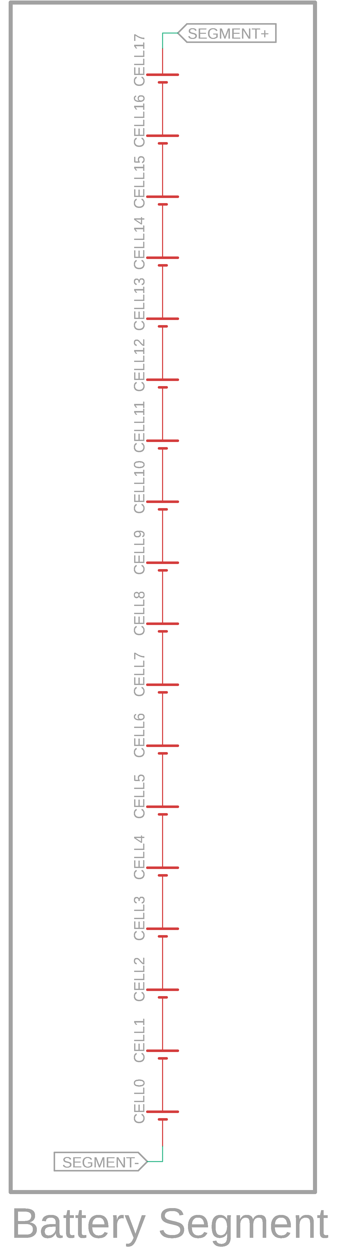
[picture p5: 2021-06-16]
ESF Schematics/Battery Segment.png

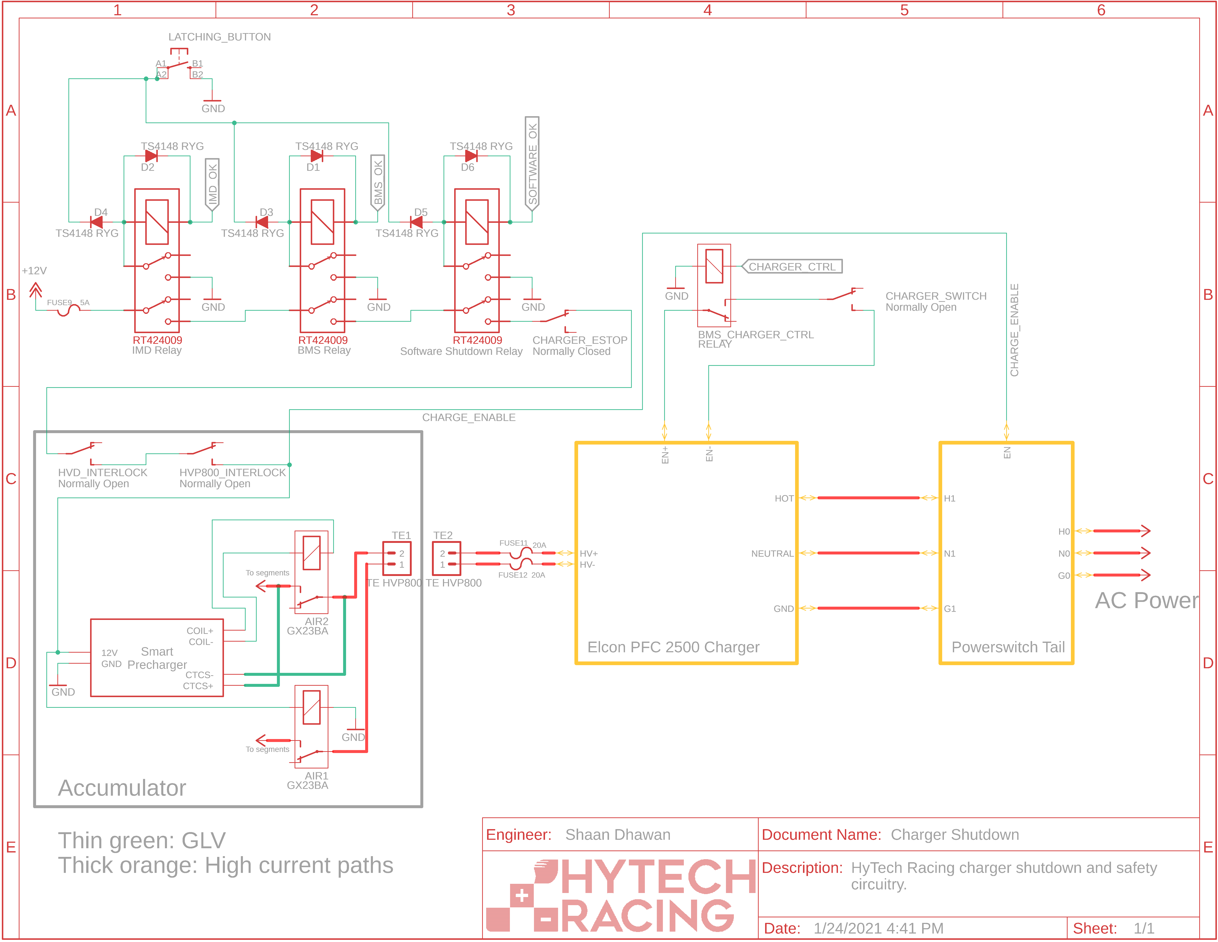
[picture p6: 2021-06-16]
ESF Schematics/Charger Shutdown.png

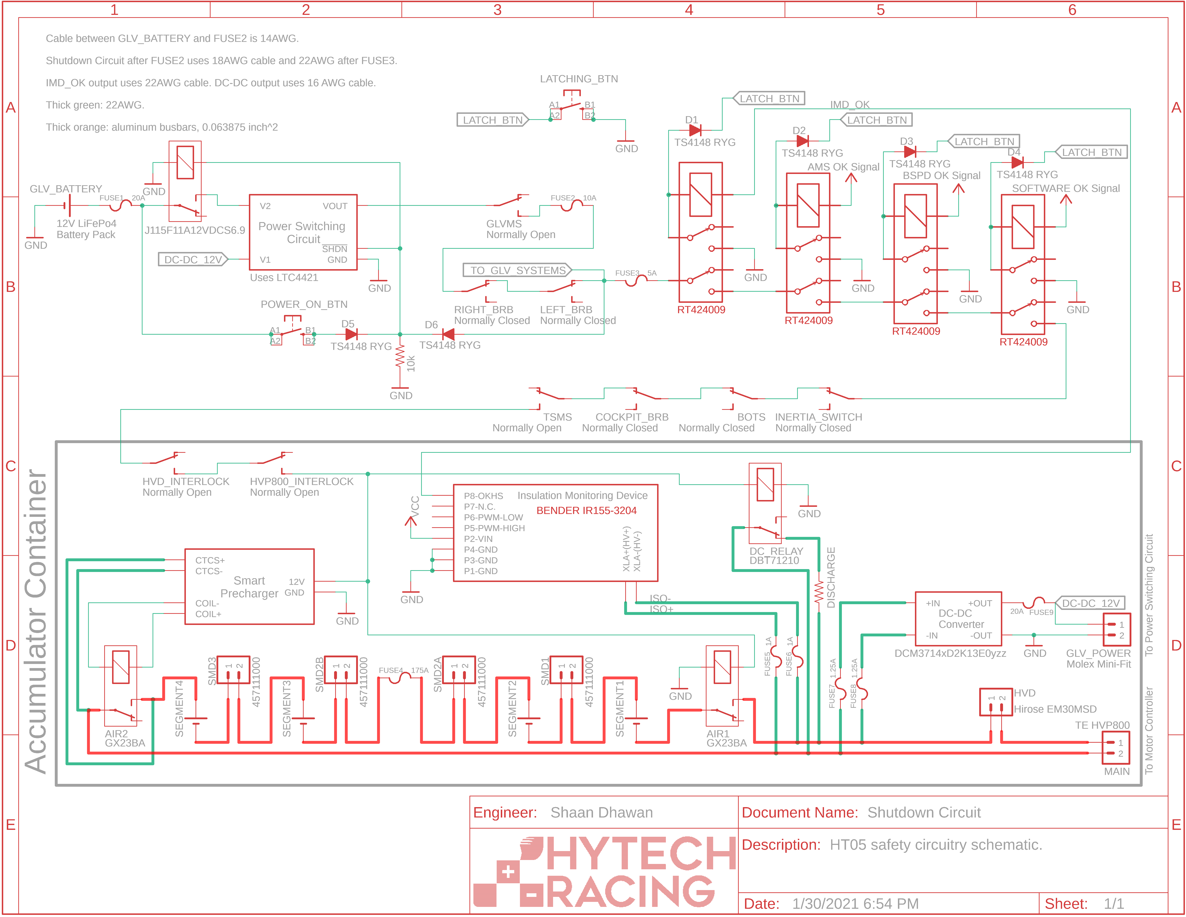
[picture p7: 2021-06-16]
ESF Schematics/Shutdown Circuit.png

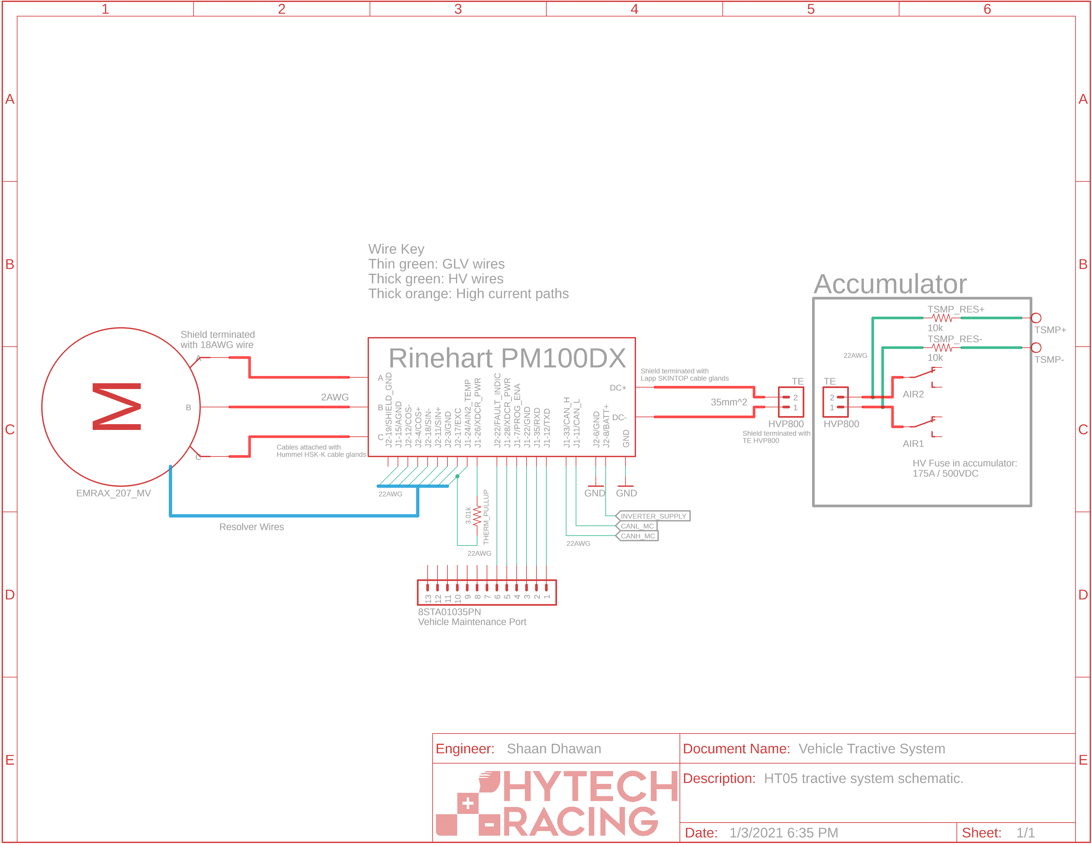
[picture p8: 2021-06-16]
ESF Schematics/Vehicle Tractive System.png

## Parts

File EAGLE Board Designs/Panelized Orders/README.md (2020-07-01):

1. Place boards at least 5mm apart so that a 1mm router can cut them out with plenty of clearance.
2. Place 4 or more holes around each board (.059” diameter) to be used as fiducials. Don't place them too close to the edge, otherwise they may be covered by tape during the depanelization milling procedure.
3. Each board will be cut out individually and be mindful of the max board size.

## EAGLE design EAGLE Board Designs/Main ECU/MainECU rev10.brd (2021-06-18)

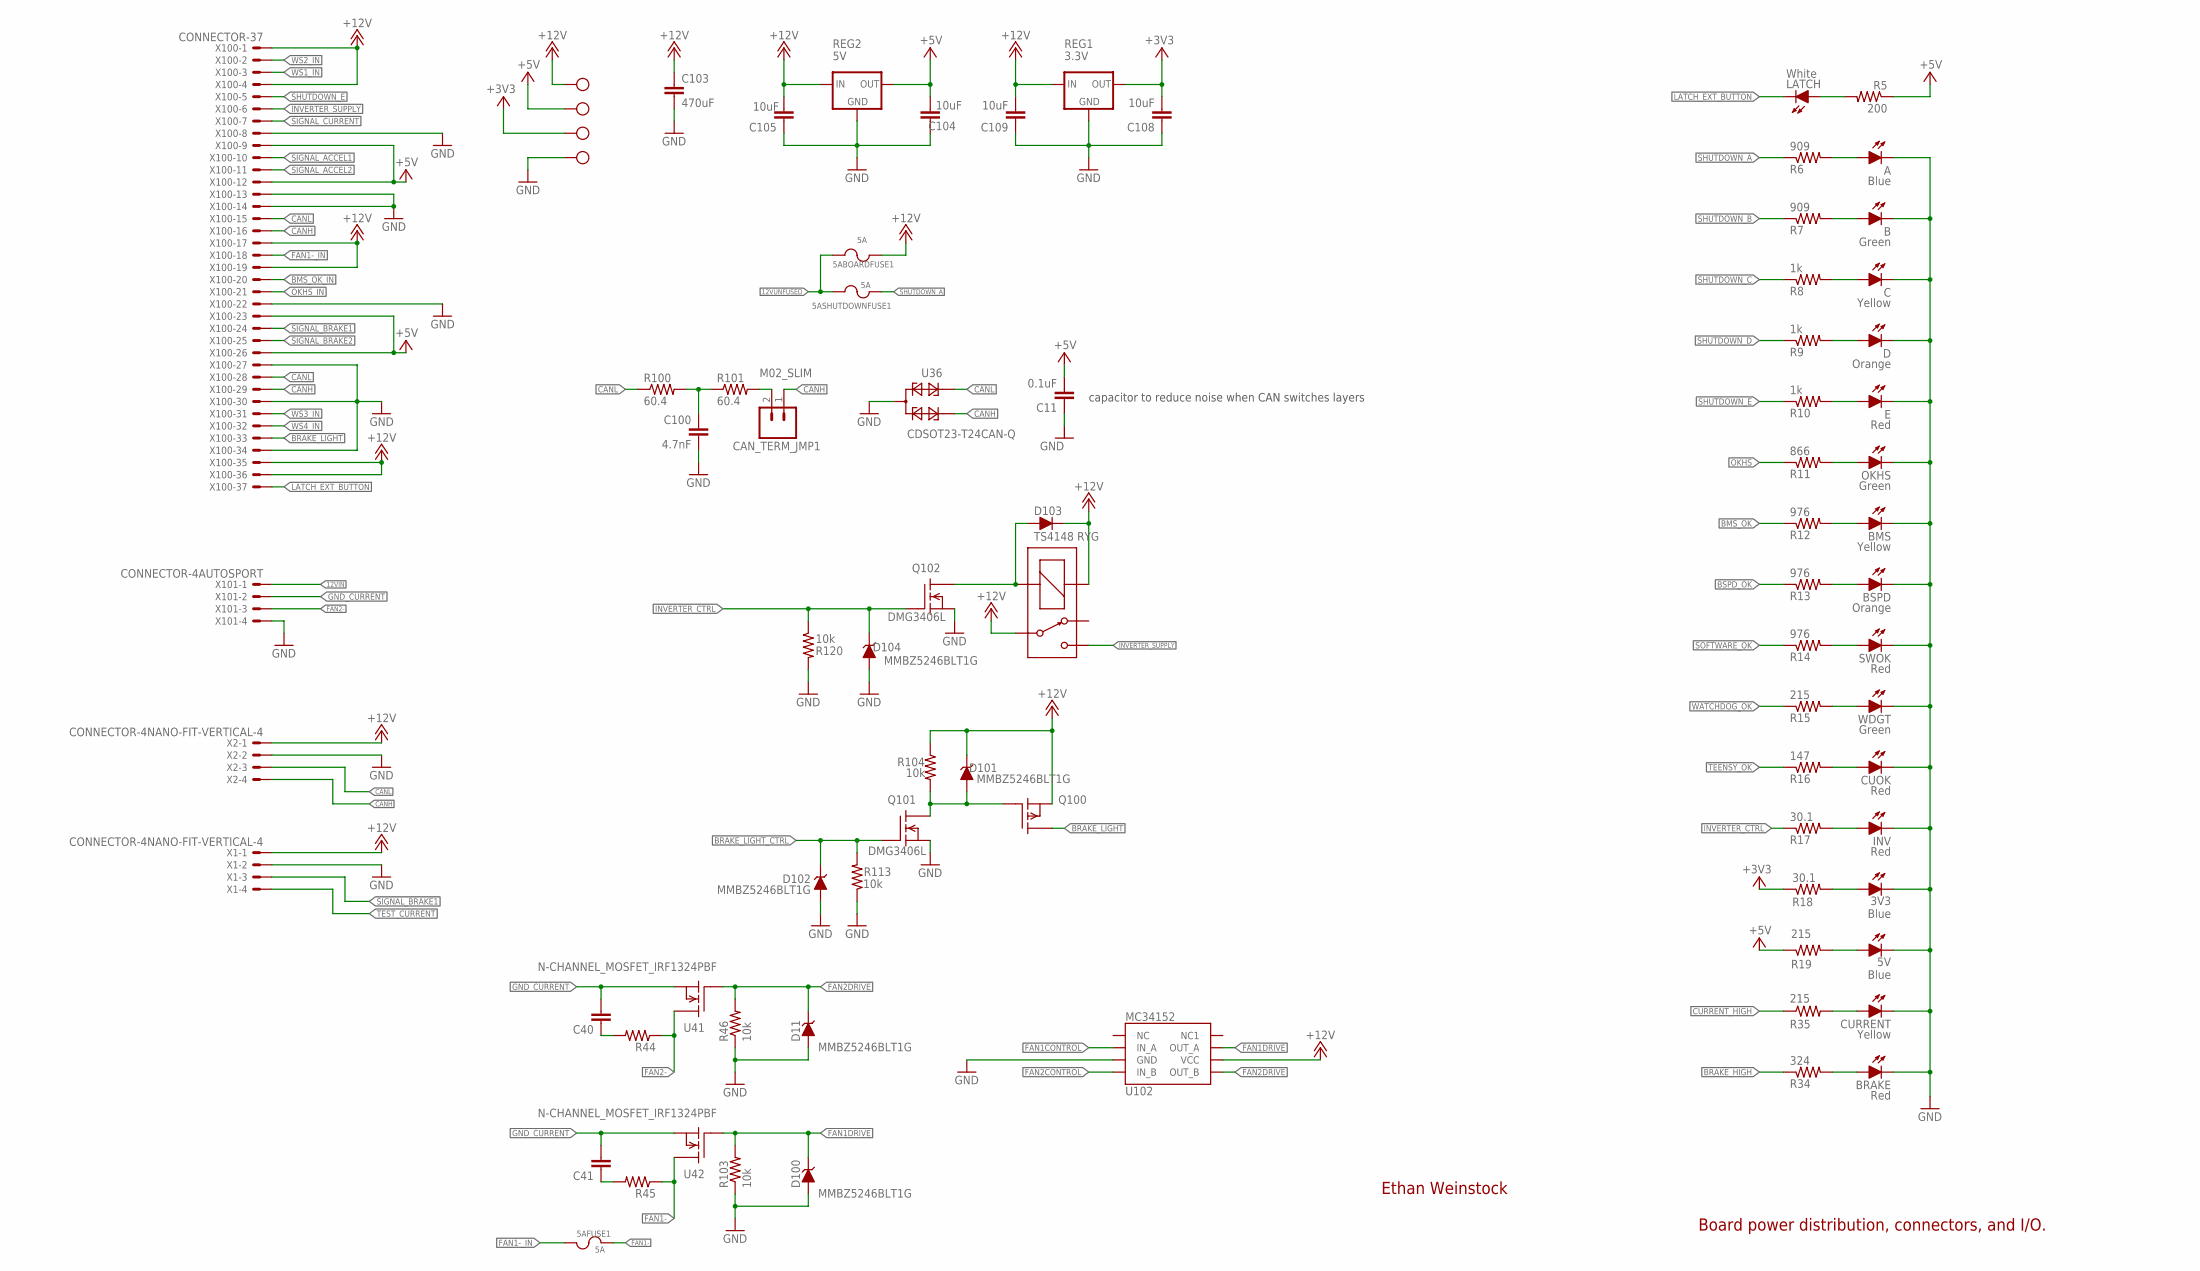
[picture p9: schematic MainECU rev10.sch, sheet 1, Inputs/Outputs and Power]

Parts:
3V3, 5V: Blue; LED-805
3V3_TEST: TEST_POINTMICRO_MINIATURE; MICRO_MINIATURE
5ABOARDFUSE1, 5AFUSE1, 5ASHUTDOWNFUSE1: 5A; MINI-BLADE_FUSE_HOLDER
12V_TEST: 12V_TEST; MICRO_MINIATURE
A: Blue; LED-805
B: Green; LED-805
BMS: Yellow; LED-805
BRAKE: Red; LED-805
BSPD: Orange; LED-805
C: Yellow; LED-805
C11: 0.1uF; 0603-CAP
C40, C41: CAP0603-CAP; 0603-CAP
C100: 4.7nF; 0603-CAP
C103: 470uF; CAP-PTH-LARGE
C104, C105, C108, C109: 10uF; 0603-CAP
CAN_TERM_JMP1: M02_SLIM; 1X02_SLIM
CUOK: Red; LED-805
CURRENT: Yellow; LED-805
D: Orange; LED-805
D11, D100, D101, D102, D104: MMBZ5246BLT1G; SOT23
D103: TS4148 RYG; 0805_D
E: Red; LED-805
INV: Red; LED-805
INVERTER_PWR_RELAY1: G5LE; ZF112
LATCH: White; LED-805
OKHS: Green; LED-805
Q100: P-CHANNEL_MOSFET_DMP3099L-7; SOT23
Q101, Q102: DMG3406L; SOT23
R5: 200; 0603-RES
R6, R7: 909; 0603-RES
R8, R9, R10: 1k; 0603-RES
R11: 866; 0603-RES
R12, R13, R14: 976; 0603-RES
R15, R19, R35: 215; 0603-RES
R16: 147; 0603-RES
R17, R18: 30.1; 0603-RES
R34: 324; 0603-RES
R44, R45: RESISTOR0603; 0603-RES
R46, R103, R104, R113, R120: 10k; 0603-RES
R100, R101: 60.4; 0603-RES
REG1: 3.3V; OKI-78SR
REG2: 5V; OKI-78SR
SWOK: Red; LED-805
U36: CDSOT23-T24CAN-Q; SOT23
U40, U43: TEST_POINTMICRO_MINIATURE; MICRO_MINIATURE
U41, U42: N-CHANNEL_MOSFET_IRF1324PBF; TO-220-H-HOLE
U102: MC34152; SOIC-08
WDGT: Green; LED-805
X1, X2: CONNECTOR-4NANO-FIT-VERTICAL-4; NANO-FIT_VERTICAL-4
X100: CONNECTOR-37; AUTOSPORT_14-35
X101: CONNECTOR-4AUTOSPORT; AUTOSPORT_12-04

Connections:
12VIN: X101.P$1; also elsewhere on the board
12VUNFUSED: 5ABOARDFUSE1.L1 (1), 5ABOARDFUSE1.L2 (1), 5ASHUTDOWNFUSE1.L1 (1), 5ASHUTDOWNFUSE1.L2 (1); also elsewhere on the board
+3V3: 3V3_TEST.P$1, C108.2, R18.1, REG1.3 (OUT); also elsewhere on the board
+5V: C11.2, C104.2, R5.1, R19.1, REG2.3 (OUT), U43.P$1, X100.P$9, X100.P$12, X100.P$23, X100.P$26; also elsewhere on the board
+12V: 5ABOARDFUSE1.R1 (2), 5ABOARDFUSE1.R2 (2), 12V_TEST.P$1, C103.1, C105.2, C109.2, D101.3 (C), D103.C, INVERTER_PWR_RELAY1.1 (COIL+), INVERTER_PWR_RELAY1.P, Q100.2 (S), R104.1, REG1.1 (IN), REG2.1 (IN), U102.6 (VCC), X1.P$1, X2.P$1, X100.P$1, X100.P$4, X100.P$17, X100.P$19, X100.P$35, X100.P$36; also elsewhere on the board
BMS_OK: R12.1; also elsewhere on the board
BMS_OK_IN: X100.P$20; also elsewhere on the board
BRAKE_HIGH: R34.1; also elsewhere on the board
BRAKE_LIGHT: Q100.3 (D), X100.P$33
BRAKE_LIGHT_CTRL: D102.3 (C), Q101.1 (G), R113.2; also elsewhere on the board
BSPD_OK: R13.1; also elsewhere on the board
CANH: CAN_TERM_JMP1.1, U36.2, X2.P$4, X100.P$16, X100.P$29; also elsewhere on the board
CANL: R100.1, U36.1, X2.P$3, X100.P$15, X100.P$28; also elsewhere on the board
CURRENT_HIGH: R35.1; also elsewhere on the board
FAN1-: 5AFUSE1.R1 (2), 5AFUSE1.R2 (2), R45.1, U42.2 (D)
FAN1-_IN: 5AFUSE1.L1 (1), 5AFUSE1.L2 (1), X100.P$18
FAN1CONTROL: U102.2 (IN_A); also elsewhere on the board
FAN1DRIVE: D100.3 (C), R103.2, U42.1 (G), U102.7 (OUT_A)
FAN2-: R44.1, U41.2 (D), X101.P$3
FAN2CONTROL: U102.4 (IN_B); also elsewhere on the board
FAN2DRIVE: D11.3 (C), R46.2, U41.1 (G), U102.5 (OUT_B)
GND: 3V3.C, 5V.C, A.C, B.C, BMS.C, BRAKE.C, BSPD.C, C.C, C11.1, C100.2, C103.2, C104.1, C105.1, C108.1, C109.1, CUOK.C, CURRENT.C, D.C, D11.1 (A), D100.1 (A), D102.1 (A), D104.1 (A), E.C, INV.C, OKHS.C, Q101.2 (S), Q102.2 (S), R46.1, R103.1, R113.1, R120.2, REG1.2 (GND), REG2.2 (GND), SWOK.C, U36.3, U40.P$1, U102.3 (GND), WDGT.C, X1.P$2, X2.P$2, X100.P$8, X100.P$13, X100.P$14, X100.P$22, X100.P$27, X100.P$30, X100.P$34, X101.P$4; also elsewhere on the board
GND_CURRENT: C40.2, C41.2, U41.3 (S), U42.3 (S), X101.P$2; also elsewhere on the board
INVERTER_CTRL: D104.3 (C), Q102.1 (G), R17.1, R120.1; also elsewhere on the board
INVERTER_SUPPLY: INVERTER_PWR_RELAY1.S, X100.P$6
LATCH_EXT_BUTTON: LATCH.C, X100.P$37; also elsewhere on the board
unnamed: E.A, R10.2
unnamed: R14.2, SWOK.A
unnamed: R15.2, WDGT.A
unnamed: CUOK.A, R16.2
unnamed: A.A, R6.2
unnamed: 3V3.A, R18.2
unnamed: C40.1, R44.2
unnamed: C41.1, R45.2
unnamed: B.A, R7.2
unnamed: C.A, R8.2
unnamed: LATCH.A, R5.2
unnamed: OKHS.A, R11.2
unnamed: BMS.A, R12.2
unnamed: CURRENT.A, R35.2
unnamed: BRAKE.A, R34.2
unnamed: BSPD.A, R13.2
unnamed: 5V.A, R19.2
unnamed: D101.1 (A), Q100.1 (G), Q101.3 (D), R104.2
unnamed: D.A, R9.2
unnamed: INV.A, R17.2
unnamed: D103.A, INVERTER_PWR_RELAY1.2 (COIL-), Q102.3 (D)
unnamed: CAN_TERM_JMP1.2, R101.2
unnamed: C100.1, R100.2, R101.1
OKHS: R11.1; also elsewhere on the board
OKHS_IN: X100.P$21; also elsewhere on the board
SHUTDOWN_A: 5ASHUTDOWNFUSE1.R1 (2), 5ASHUTDOWNFUSE1.R2 (2), R6.1; also elsewhere on the board
SHUTDOWN_B: R7.1; also elsewhere on the board
SHUTDOWN_C: R8.1; also elsewhere on the board
SHUTDOWN_D: R9.1; also elsewhere on the board
SHUTDOWN_E: R10.1, X100.P$5; also elsewhere on the board
SIGNAL_ACCEL1: X100.P$10; also elsewhere on the board
SIGNAL_ACCEL2: X100.P$11; also elsewhere on the board
SIGNAL_BRAKE1: X1.P$3, X100.P$24; also elsewhere on the board
SIGNAL_BRAKE2: X100.P$25; also elsewhere on the board
SIGNAL_CURRENT: X100.P$7; also elsewhere on the board
SOFTWARE_OK: R14.1; also elsewhere on the board
TEENSY_OK: R16.1; also elsewhere on the board
TEST_CURRENT: X1.P$4; also elsewhere on the board
WATCHDOG_OK: R15.1; also elsewhere on the board
WS1_IN: X100.P$3; also elsewhere on the board
WS2_IN: X100.P$2; also elsewhere on the board
WS3_IN: X100.P$31; also elsewhere on the board
WS4_IN: X100.P$32; also elsewhere on the board

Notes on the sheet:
Ethan Weinstock
Board power distribution, connectors, and I/O.
capacitor to reduce noise when CAN switches layers

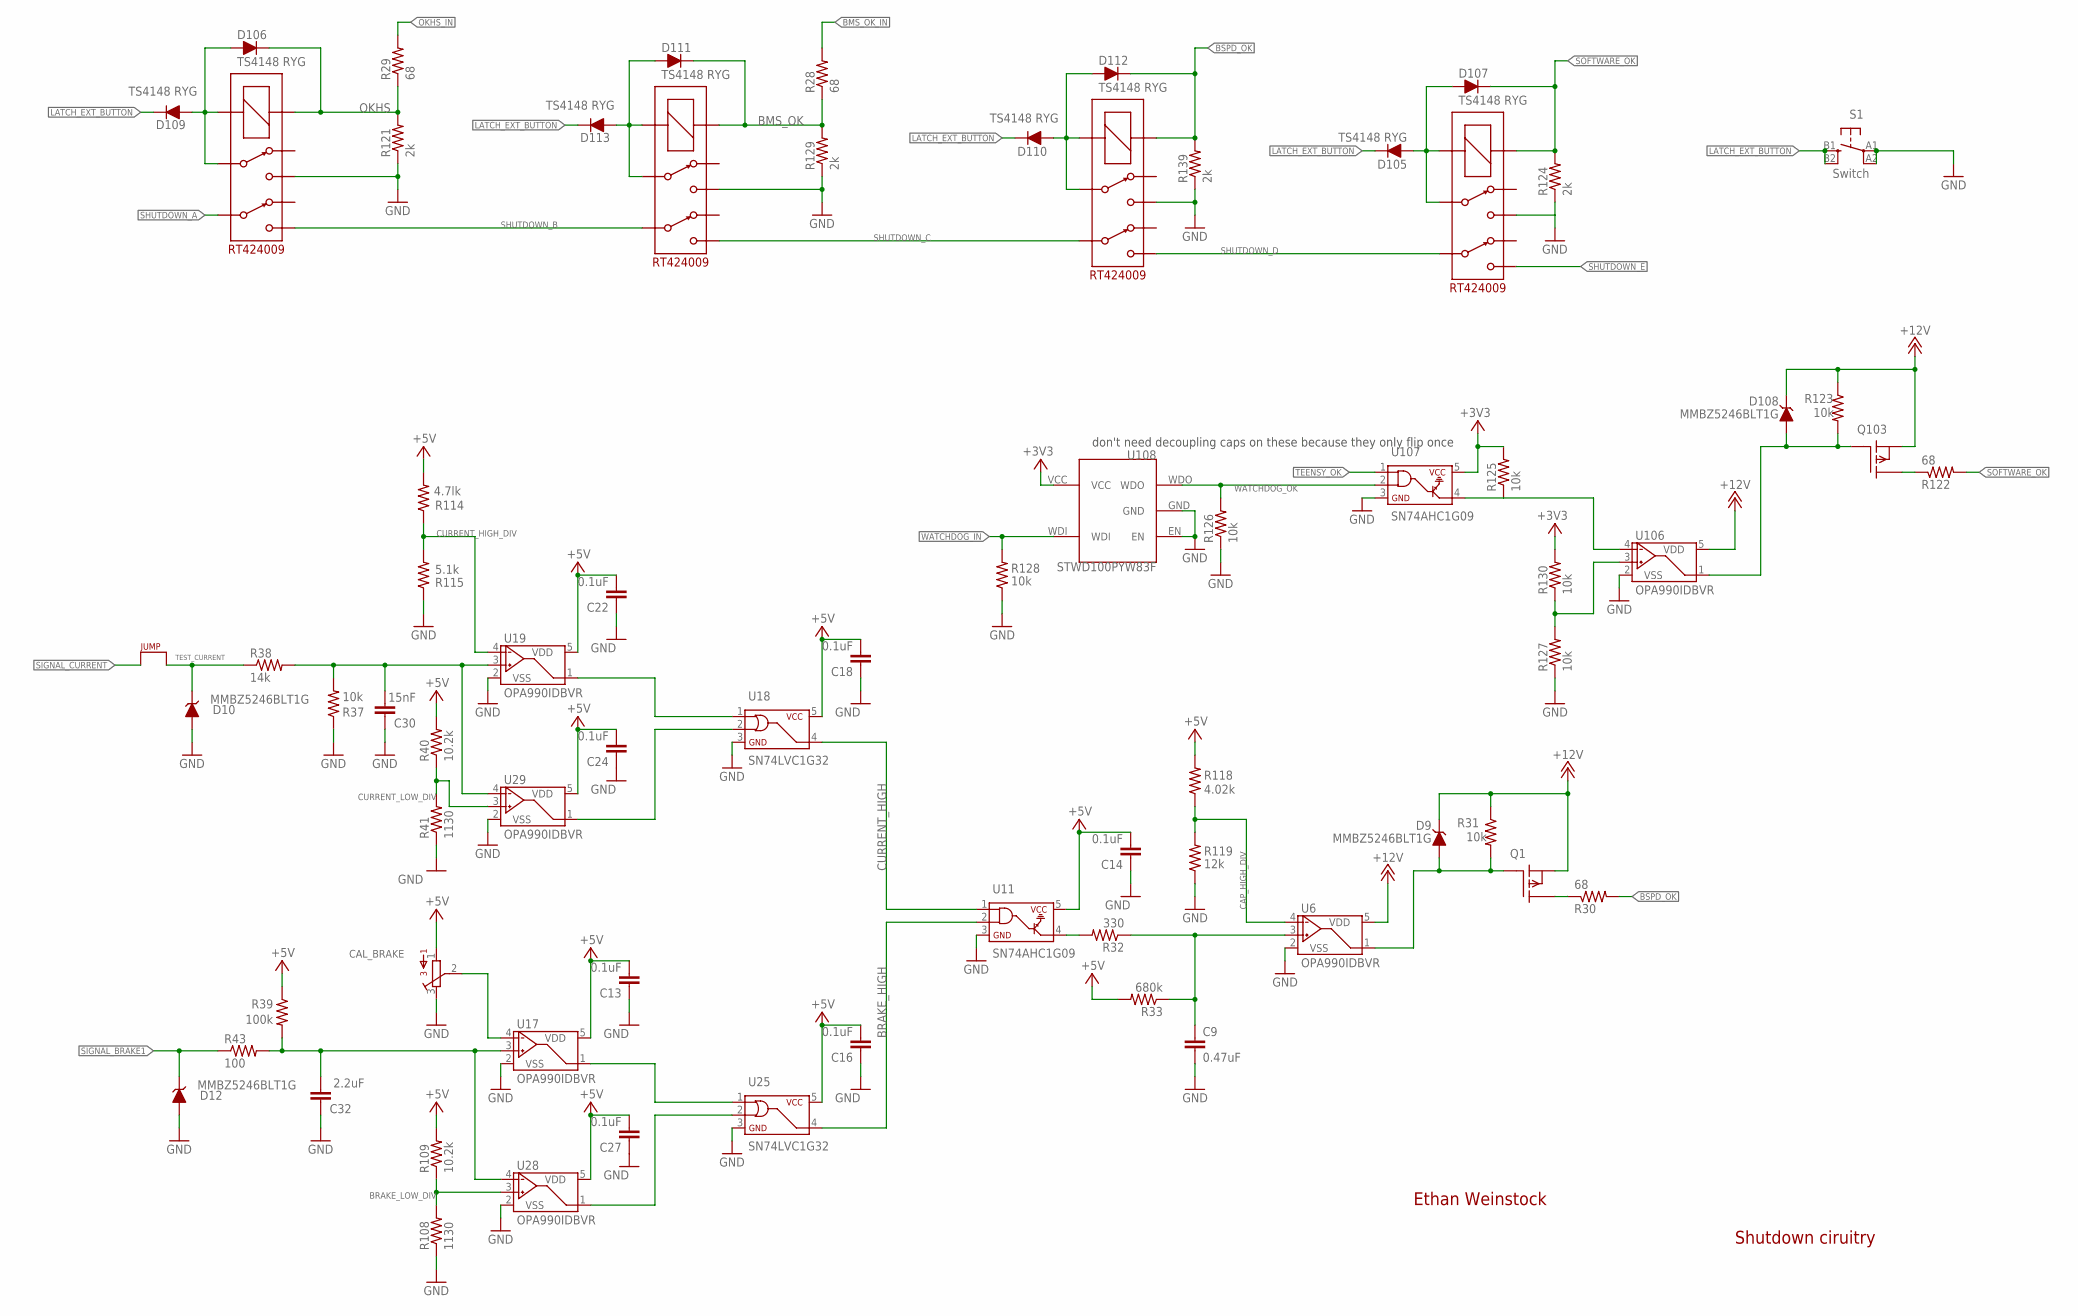
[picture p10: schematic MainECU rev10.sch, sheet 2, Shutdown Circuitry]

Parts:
C9: 0.47uF; 0603-CAP
C13, C14, C16, C18, C22, C24, C27: 0.1uF; 0603-CAP
C30: 15nF; 0603-CAP
C32: 2.2uF; 0603-CAP
CAL_BRAKE: TRIMPOT_3296C; TRIMPOT_3296
D9, D10, D12, D108: MMBZ5246BLT1G; SOT23
D105, D106, D107, D109, D110, D111, D112, D113: TS4148 RYG; 0805_D
IMD_SHUTDOWN_RLY1: RT424009; RELAY_DPDT
J1: JUMPER.1; 1X02
Q1, Q103: P-CHANNEL_MOSFET_DMP3099L-7; SOT23
R28, R29, R30, R122: 68; 0603-RES
R31, R37, R123, R125, R126, R127, R128, R130: 10k; 0603-RES
R32: 330; 0603-RES
R33: 680k; 0603-RES
R38: 14k; 0603-RES
R39: 100k; 0603-RES
R40, R109: 10.2k; 0603-RES
R41, R108: 1130; 0603-RES
R43: 100; 0603-RES
R114: 4.7lk; 0603-RES
R115: 5.1k; 0603-RES
R118: 4.02k; 0603-RES
R119: 12k; 0603-RES
R121, R124, R129, R139: 2k; 0603-RES
S1: Switch; TACTILE_SWITCH_SMD_6.2MM_TALL
U2, U3, U4: RT424009; RELAY_DPDT
U6, U17, U19, U28, U29, U106: OPA990IDBVR; SOT-23-5
U11, U107: SN74AHC1G09; SOT-23-5
U18, U25: SN74LVC1G32; SOT-23-5
U108: STWD100PYW83F; SOT323-5

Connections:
+3V3: R125.2, R130.2, U107.5, U108.VCC; also elsewhere on the board
+5V: C13.2, C14.2, C16.2, C18.2, C22.2, C24.2, C27.2, CAL_BRAKE.1, R33.2, R39.1, R40.2, R109.2, R114.2, R118.2, U11.5, U17.5 (VDD), U18.5 (VCC), U19.5 (VDD), U25.5 (VCC), U28.5 (VDD), U29.5 (VDD); also elsewhere on the board
+12V: D9.3 (C), D108.3 (C), Q1.2 (S), Q103.2 (S), R31.1, R123.1, U6.5 (VDD), U106.5 (VDD); also elsewhere on the board
BMS_OK: D111.C, R28.1, R129.2, U3.COIL+; also elsewhere on the board
BMS_OK_IN: R28.2; also elsewhere on the board
BMS_PWR_STEP1: D111.A, D113.A, U3.3, U3.COIL-
BRAKE_HIGH: U11.2, U25.4 (Y); also elsewhere on the board
BRAKE_LOW_DIV: R108.2, R109.1, U28.3 (VIN+)
BSPD_OK: D112.C, R30.2, R139.2, U2.COIL+; also elsewhere on the board
CAP_HIGH_DIV: R118.1, R119.2, U6.4 (VIN-)
CURRENT_HIGH: U11.1, U18.4 (Y); also elsewhere on the board
CURRENT_HIGH_DIV: R114.1, R115.2, U19.4 (VIN-)
CURRENT_LOW_DIV: R40.1, R41.2, U29.3 (VIN+)
GND: C9.2, C13.1, C14.1, C16.1, C18.1, C22.1, C24.1, C27.1, C30.1, C32.1, CAL_BRAKE.3, D10.1 (A), D12.1 (A), IMD_SHUTDOWN_RLY1.4, R37.1, R41.1, R108.1, R115.1, R119.1, R121.1, R124.1, R126.1, R127.1, R128.1, R129.1, R139.1, S1.A1, S1.A2 (P1), U2.4, U3.4, U4.4, U6.2 (VSS), U11.3, U17.2 (VSS), U18.3 (GND), U19.2 (VSS), U25.3 (GND), U28.2 (VSS), U29.2 (VSS), U106.2 (VSS), U107.3, U108.EN, U108.GND; also elsewhere on the board
IMD_PWR_STEP1: D106.A, D109.A, IMD_SHUTDOWN_RLY1.3, IMD_SHUTDOWN_RLY1.COIL-
LATCH_EXT_BUTTON: D105.C, D109.C, D110.C, D113.C, S1.B1 (S), S1.B2 (S1); also elsewhere on the board
unnamed: Q1.3 (D), R30.1
unnamed: C32.2, R39.2, R43.2, U17.3 (VIN+), U28.4 (VIN-)
unnamed: U17.1 (VOUT), U25.1 (A)
unnamed: D105.A, D107.A, U4.3, U4.COIL-
unnamed: U25.2 (B), U28.1 (VOUT)
unnamed: D108.1 (A), Q103.1 (G), R123.2, U106.1 (VOUT)
unnamed: Q103.3 (D), R122.1
unnamed: CAL_BRAKE.2, U17.4 (VIN-)
unnamed: U18.1 (A), U19.1 (VOUT)
unnamed: U18.2 (B), U29.1 (VOUT)
unnamed: R125.1, U106.4 (VIN-), U107.4
unnamed: R127.2, R130.1, U106.3 (VIN+)
unnamed: D110.A, D112.A, U2.3, U2.COIL-
unnamed: C30.2, R37.2, R38.2, U19.3 (VIN+), U29.4 (VIN-)
unnamed: R32.2, U11.4
unnamed: C9.1, R32.1, R33.1, U6.3 (VIN+)
unnamed: D9.1 (A), Q1.1 (G), R31.2, U6.1 (VOUT)
OKHS: D106.C, IMD_SHUTDOWN_RLY1.COIL+, R29.1, R121.2; also elsewhere on the board
OKHS_IN: R29.2; also elsewhere on the board
SHUTDOWN_A: IMD_SHUTDOWN_RLY1.6; also elsewhere on the board
SHUTDOWN_B: IMD_SHUTDOWN_RLY1.5, U3.6; also elsewhere on the board
SHUTDOWN_C: U2.6, U3.5; also elsewhere on the board
SHUTDOWN_D: U2.5, U4.6; also elsewhere on the board
SHUTDOWN_E: U4.5; also elsewhere on the board
SIGNAL_BRAKE1: D12.3 (C), R43.1; also elsewhere on the board
SIGNAL_CURRENT: J1.1; also elsewhere on the board
SOFTWARE_OK: D107.C, R122.2, R124.2, U4.COIL+; also elsewhere on the board
TEENSY_OK: U107.1; also elsewhere on the board
TEST_CURRENT: D10.3 (C), J1.2, R38.1; also elsewhere on the board
WATCHDOG_IN: R128.2, U108.WDI; also elsewhere on the board
WATCHDOG_OK: R126.2, U107.2, U108.WDO; also elsewhere on the board

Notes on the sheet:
Ethan Weinstock
Shutdown ciruitry
don't need decoupling caps on these because they only flip once

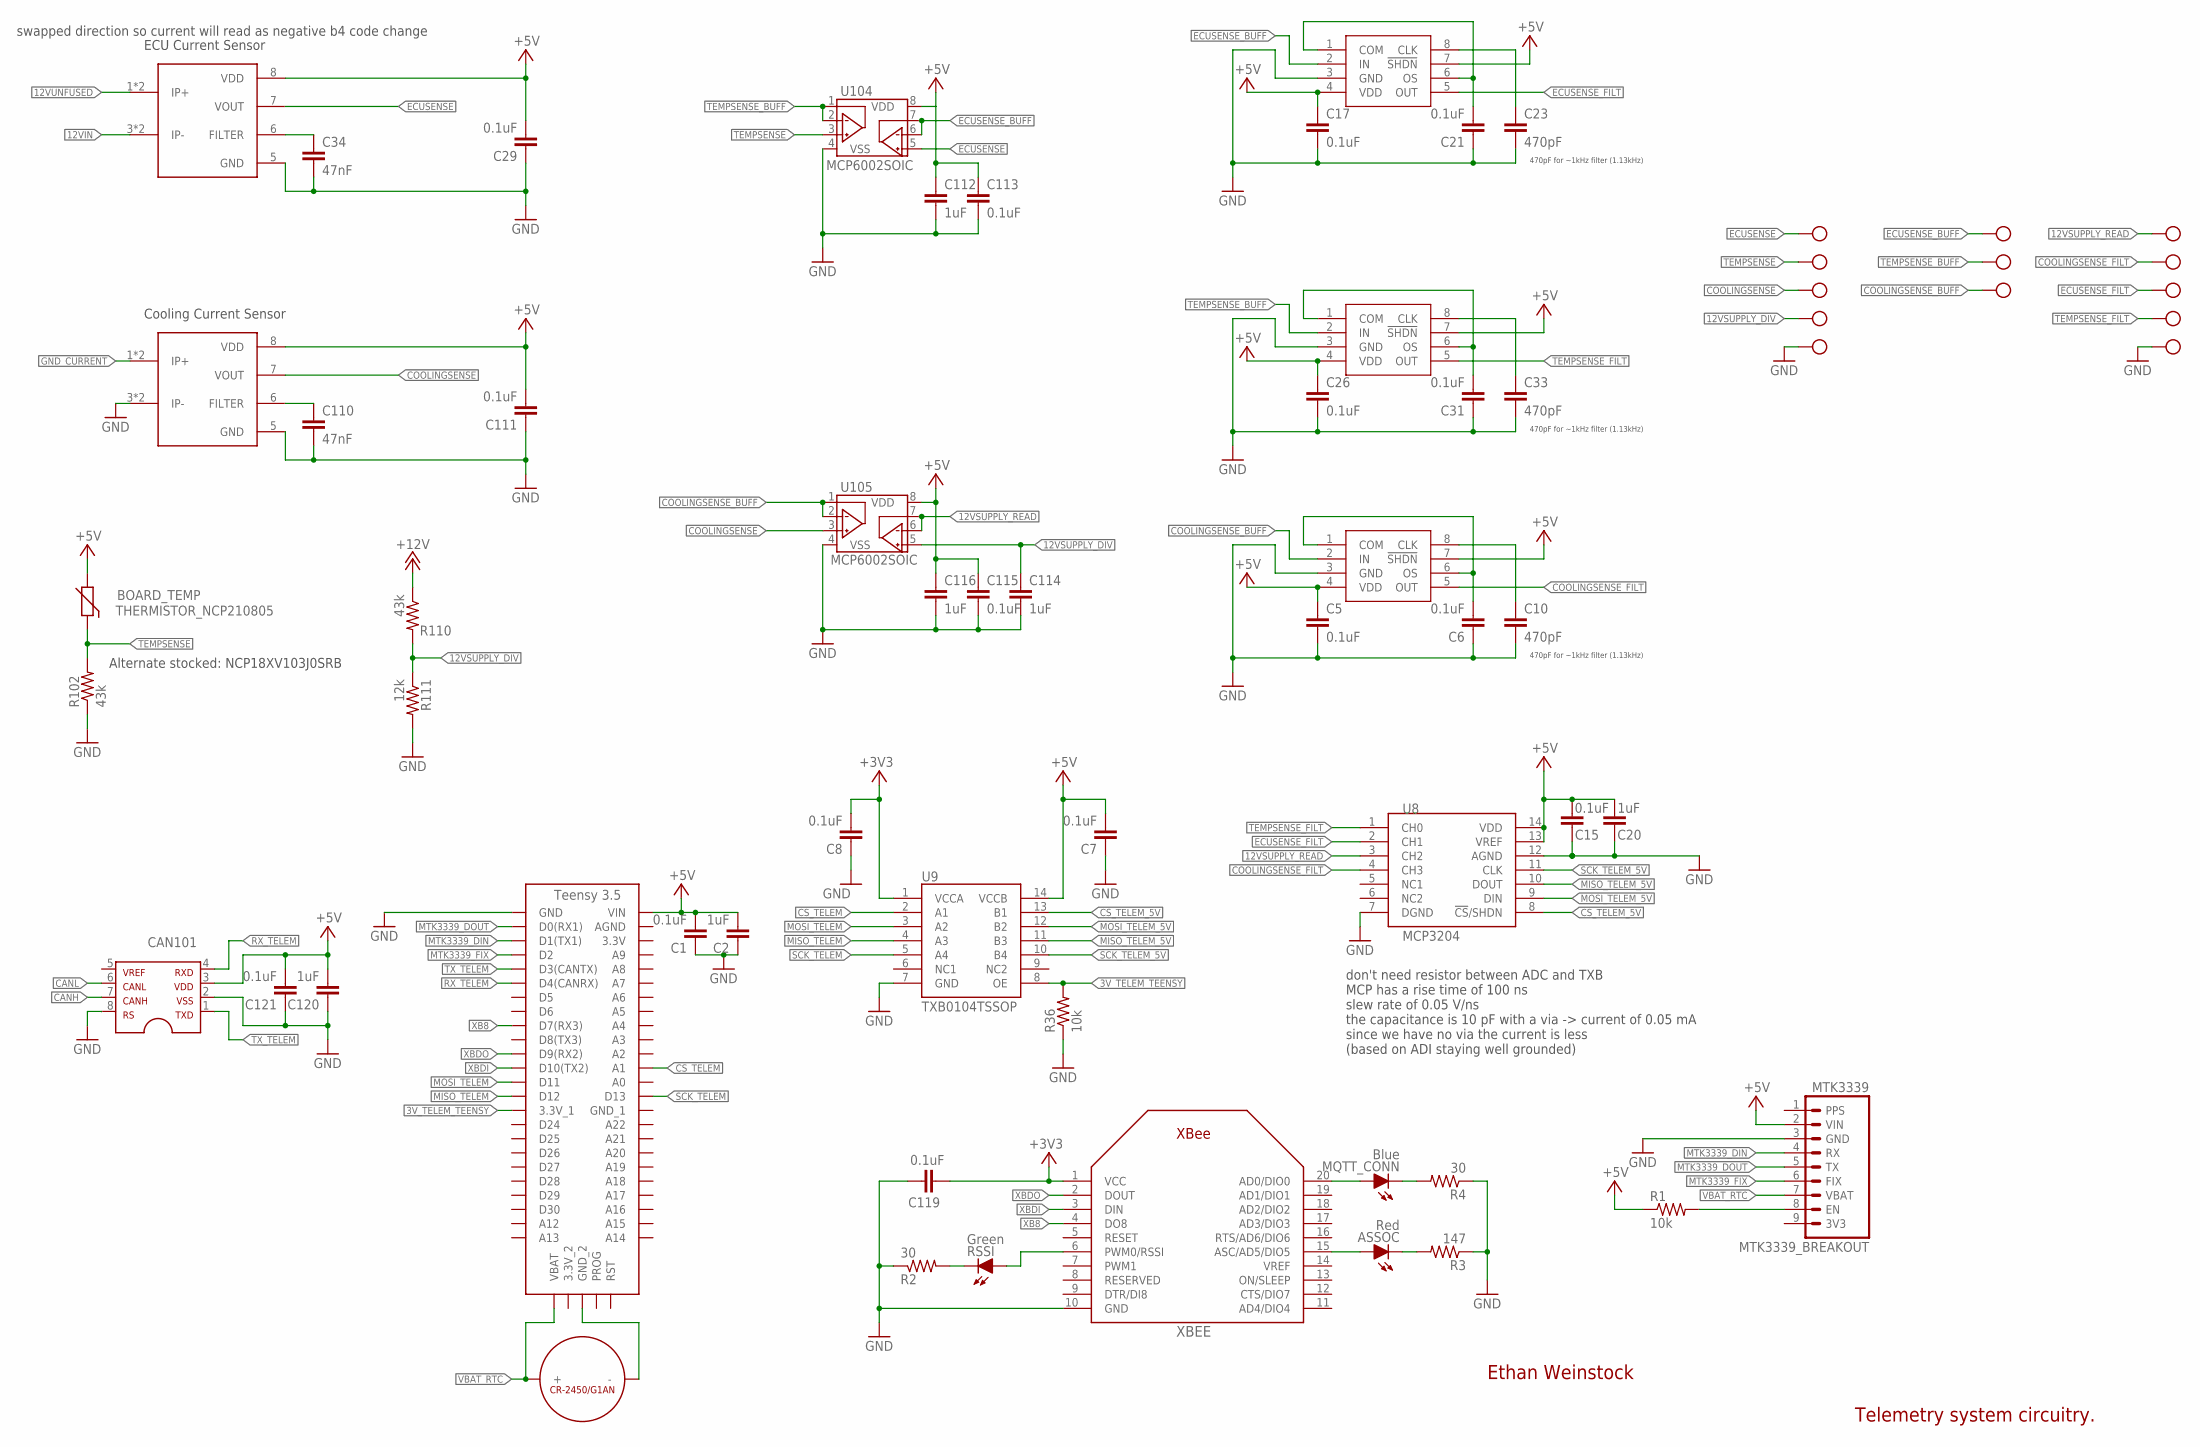
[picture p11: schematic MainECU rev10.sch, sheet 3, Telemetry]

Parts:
ASSOC: Red; LED-805
BOARD_TEMP: THERMISTOR_NCP210805; 0805
C1, C5, C6, C7, C8, C15, C17, C21, C26, C29, C31, C111, C113, C115, C119, C121: 0.1uF; 0603-CAP
C2, C20, C112, C114, C116, C120: 1uF; 0603-CAP
C10, C23, C33: 470pF; 0603-CAP
C34, C110: 47nF; 0603-CAP
CAN101: MCP2551; SOIC-08
MQTT_CONN: Blue; LED-805
MTK3339_BREAKOUT: MTK3339; 1X09
R1, R36: 10k; 0603-RES
R2, R4: 30; 0603-RES
R3: 147; 0603-RES
R102, R110: 43k; 0603-RES
R111: 12k; 0603-RES
RSSI: Green; LED-805
U1: TEENSY_3.5_EXT
U7, U24, U33: MAX7480; SOIC-08
U8: MCP3204; SO14
U9: TXB0104TSSOP; TSSOP-14
U12, U13, U14, U15, U16, U20, U21, U22, U26, U27, U30, U31, U32: TEST_POINTMICRO_MINIATURE; MICRO_MINIATURE
U35, U103: ACHS-7121; SOP8
U104, U105: MCP6002SOIC; SOIC-08
U109: CR-2450/G1AN
XBEE: XBEE

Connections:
3V_TELEM_TEENSY: R36.2, U1.3.3V_1, U9.8 (OE)
12VIN: U35.3 (IP-), U35.4 (IP-); also elsewhere on the board
12VSUPPLY_DIV: C114.1, R110.2, R111.1, U16.P$1, U105.5 (VINB+)
12VSUPPLY_READ: U8.3 (CH2), U15.P$1, U105.6 (VINB-), U105.7 (VOUTB)
12VUNFUSED: U35.1 (IP+), U35.2 (IP+); also elsewhere on the board
+3V3: C8.2, C119.1, U9.1 (VCCA), XBEE.1 (VCC); also elsewhere on the board
+5V: BOARD_TEMP.1, C1.2, C2.2, C5.1, C7.2, C15.2, C17.1, C20.2, C26.1, C29.2, C111.2, C112.1, C113.1, C115.1, C116.1, C120.2, C121.2, CAN101.3, MTK3339_BREAKOUT.2 (VIN), R1.1, U1.VIN, U7.4 (VDD), U7.7 (!SHDN), U8.13 (VREF), U8.14 (VDD), U9.14 (VCCB), U24.4 (VDD), U24.7 (!SHDN), U33.4 (VDD), U33.7 (!SHDN), U35.8 (VDD), U103.8 (VDD), U104.8 (VDD), U105.8 (VDD); also elsewhere on the board
+12V: R110.1; also elsewhere on the board
CANH: CAN101.7; also elsewhere on the board
CANL: CAN101.6; also elsewhere on the board
COOLINGSENSE: U21.P$1, U103.7 (VOUT), U105.3 (VINA+)
COOLINGSENSE_BUFF: U7.2 (IN), U12.P$1, U105.1 (VOUTA), U105.2 (VINA-)
COOLINGSENSE_FILT: U7.5 (OUT), U8.4 (CH3), U20.P$1
CS_TELEM: U1.A1, U9.2 (A1)
CS_TELEM_5V: U8.8 (!CS!/SHDN), U9.13 (B1)
ECUSENSE: U27.P$1, U35.7 (VOUT), U104.5 (VINB+)
ECUSENSE_BUFF: U13.P$1, U24.2 (IN), U104.6 (VINB-), U104.7 (VOUTB)
ECUSENSE_FILT: U8.2 (CH1), U24.5 (OUT), U26.P$1
GND: C1.1, C2.1, C5.2, C6.1, C7.1, C8.1, C10.2, C15.1, C17.2, C20.1, C21.1, C23.2, C26.2, C29.1, C31.1, C33.2, C34.2, C110.2, C111.1, C112.2, C113.2, C114.2, C115.2, C116.2, C119.2, C120.1, C121.1, CAN101.2, CAN101.8, MTK3339_BREAKOUT.3 (GND), R2.1, R3.1, R4.1, R36.1, R102.1, R111.2, U1.GND, U7.3 (GND), U8.7 (DGND), U8.12 (AGND), U9.7 (GND), U22.P$1, U24.3 (GND), U32.P$1, U33.3 (GND), U35.5 (GND), U103.3 (IP-), U103.4 (IP-), U103.5 (GND), U104.4 (VSS), U105.4 (VSS), XBEE.10 (GND); also elsewhere on the board
GND_CURRENT: U103.1 (IP+), U103.2 (IP+); also elsewhere on the board
MISO_TELEM: U1.D12, U9.4 (A3)
MISO_TELEM_5V: U8.10 (DOUT), U9.11 (B3)
MOSI_TELEM: U1.D11, U9.3 (A2)
MOSI_TELEM_5V: U8.9 (DIN), U9.12 (B2)
MTK3339_DIN: MTK3339_BREAKOUT.4 (RX), U1.D1(TX1)
MTK3339_DOUT: MTK3339_BREAKOUT.5 (TX), U1.D0(RX1)
MTK3339_FIX: MTK3339_BREAKOUT.6 (FIX), U1.D2
unnamed: C10.1, U7.8 (CLK)
unnamed: C6.2, U7.1 (COM), U7.6 (OS)
unnamed: C110.1, U103.6 (FILTER)
unnamed: C34.1, U35.6 (FILTER)
unnamed: R2.2, RSSI.C
unnamed: RSSI.A, XBEE.6 (PWM0/RSSI)
unnamed: ASSOC.A, XBEE.15 (ASC/AD5/DIO5)
unnamed: ASSOC.C, R3.2
unnamed: MQTT_CONN.C, R4.2
unnamed: MQTT_CONN.A, XBEE.20 (AD0/DIO0)
unnamed: U1.GND_2, U109.-
unnamed: C33.1, U33.8 (CLK)
unnamed: C23.1, U24.8 (CLK)
unnamed: MTK3339_BREAKOUT.8 (EN), R1.2
unnamed: C21.2, U24.1 (COM), U24.6 (OS)
unnamed: C31.2, U33.1 (COM), U33.6 (OS)
RX_TELEM: CAN101.4, U1.D4(CANRX)
SCK_TELEM: U1.D13, U9.5 (A4)
SCK_TELEM_5V: U8.11 (CLK), U9.10 (B4)
TEMPSENSE: BOARD_TEMP.2, R102.2, U31.P$1, U104.3 (VINA+)
TEMPSENSE_BUFF: U14.P$1, U33.2 (IN), U104.1 (VOUTA), U104.2 (VINA-)
TEMPSENSE_FILT: U8.1 (CH0), U30.P$1, U33.5 (OUT)
TX_TELEM: CAN101.1, U1.D3(CANTX)
VBAT_RTC: MTK3339_BREAKOUT.7 (VBAT), U1.VBAT, U109.+_0 (+), U109.+_1 (+)
XB8: U1.D7(RX3), XBEE.4 (DO8)
XBDI: U1.D10(TX2), XBEE.3 (DIN)
XBDO: U1.D9(RX2), XBEE.2 (DOUT)

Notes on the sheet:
ECU Current Sensor
Cooling Current Sensor
470pF for ~1kHz filter (1.13kHz)
Alternate stocked: NCP18XV103J0SRB
Ethan Weinstock
Telemetry system circuitry.
don't need resistor between ADC and TXB MCP has a rise time of 100 ns slew rate of 0.05 V/ns the capacitance is 10 pF with a via -> current of 0.05 mA since we have no via the current is less (based on ADI staying well grounded)
swapped direction so current will read as negative b4 code change

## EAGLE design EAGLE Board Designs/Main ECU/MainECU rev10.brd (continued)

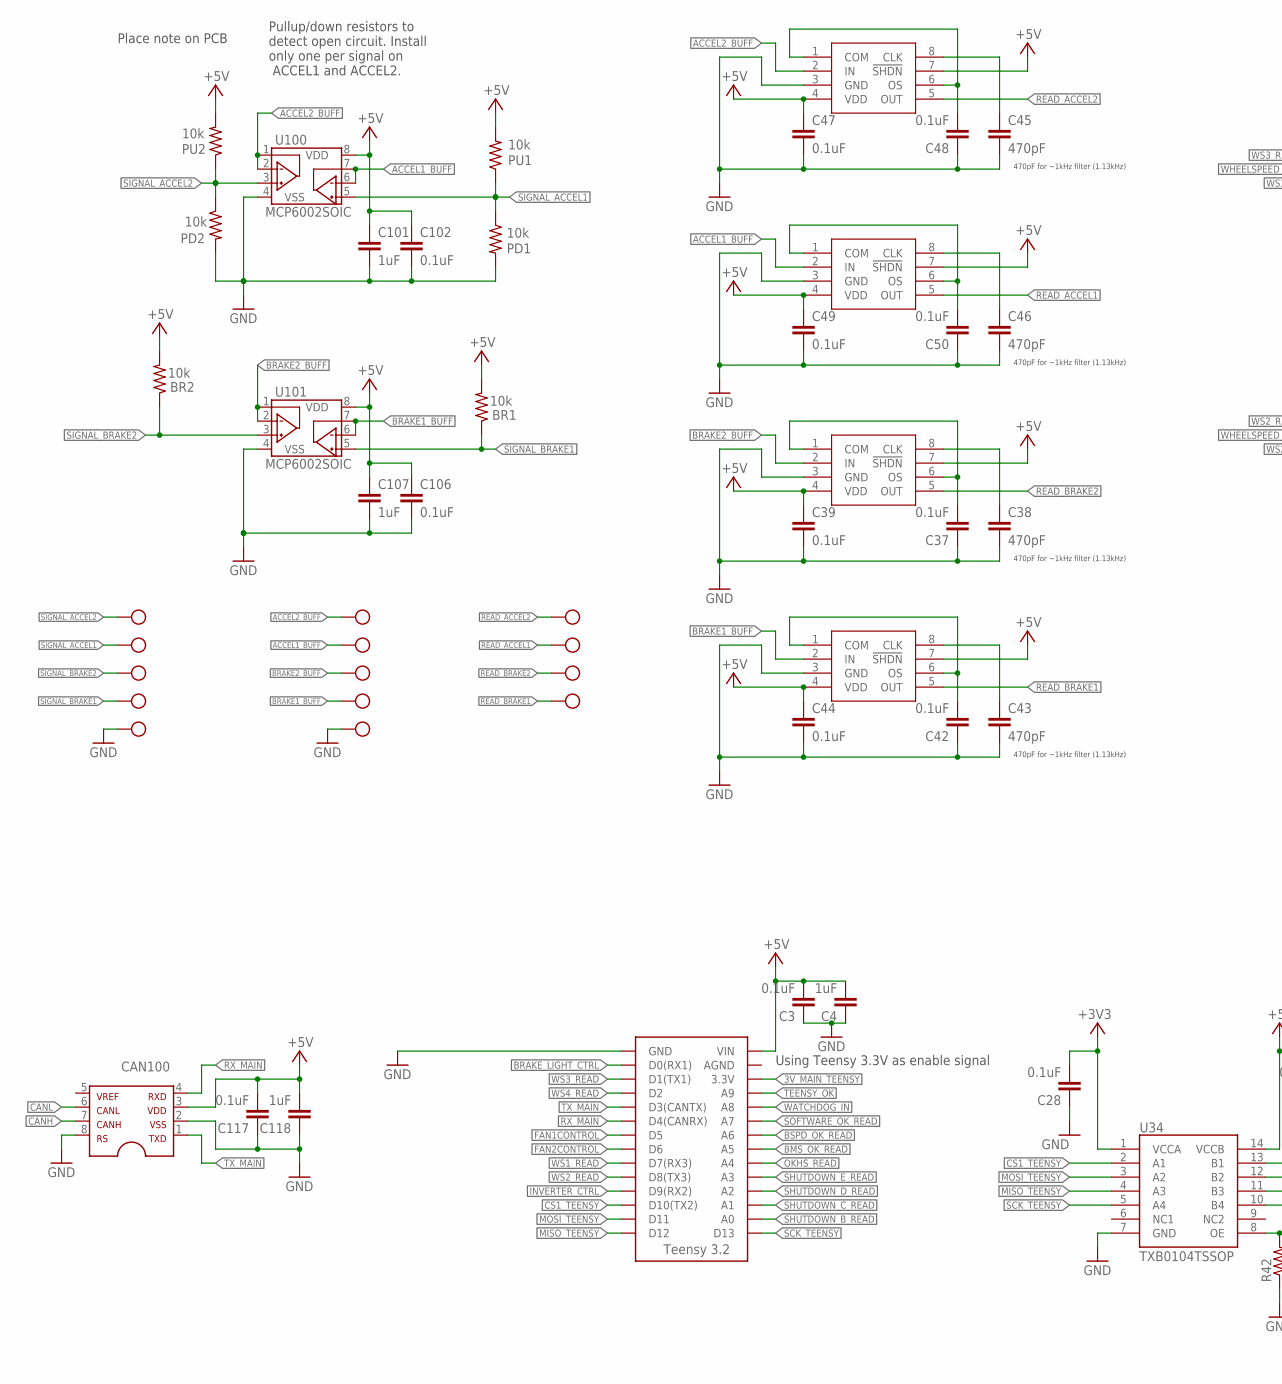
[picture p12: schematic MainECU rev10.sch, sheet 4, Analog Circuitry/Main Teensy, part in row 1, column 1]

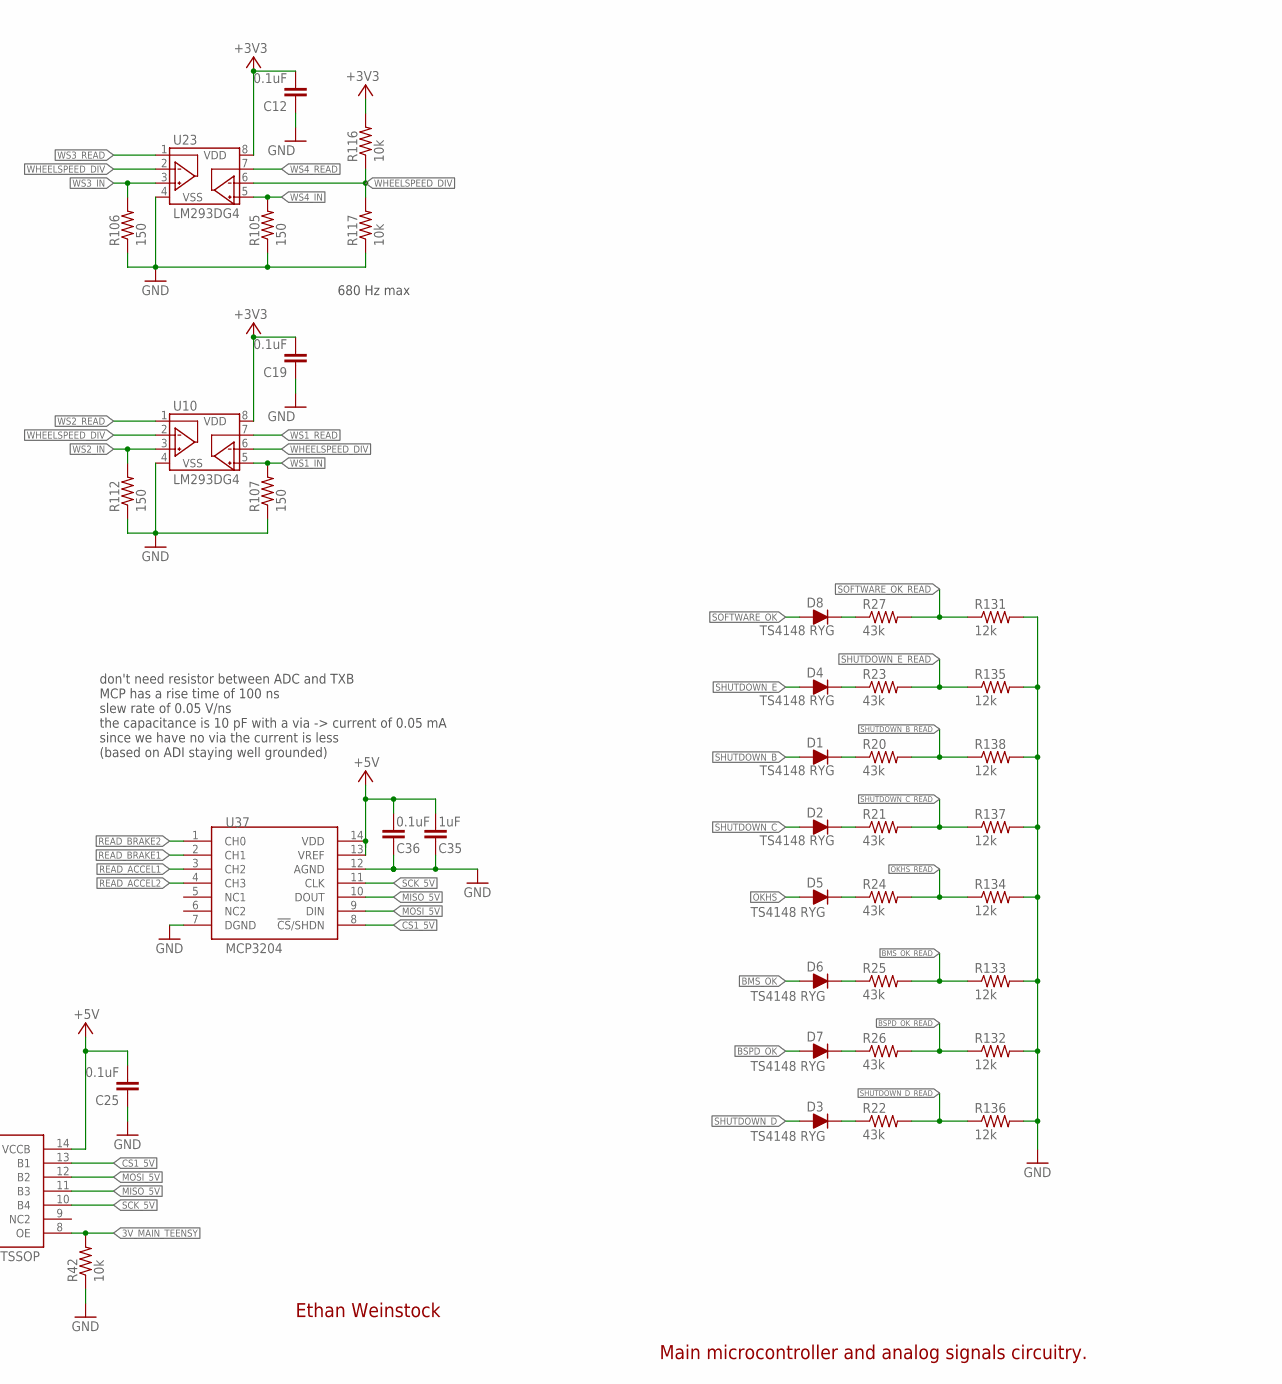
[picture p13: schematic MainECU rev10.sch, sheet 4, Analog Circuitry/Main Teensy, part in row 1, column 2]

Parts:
ACCEL1_BUFF_TEST: 12V_TEST; MICRO_MINIATURE
ACCEL2_BUFF_TEST: TEST_POINTMICRO_MINIATURE; MICRO_MINIATURE
BR1, BR2: 10k; 0603-RES
BRAKE1_BUFF_TEST, BRAKE2_BUFF_TEST: TEST_POINTMICRO_MINIATURE; MICRO_MINIATURE
C3, C12, C19, C25, C28, C36, C37, C39, C42, C44, C47, C48, C49, C50, C102, C106, C117: 0.1uF; 0603-CAP
C4, C35, C101, C107, C118: 1uF; 0603-CAP
C38, C43, C45, C46: 470pF; 0603-CAP
CAN100: MCP2551; SOIC-08
D1, D2, D3, D4, D5, D6, D7, D8: TS4148 RYG; 0805_D
PD1, PD2: 10k; 0603-RES
PU1, PU2: 10k; 0603-RES
R20, R21, R22, R23, R24, R25, R26, R27: 43k; 0603-RES
R42, R116, R117: 10k; 0603-RES
R105, R106, R107, R112: 150; 0603-RES
R131, R132, R133, R134, R135, R136, R137, R138: 12k; 0603-RES
READ_ACCEL1_TEST: 12V_TEST; MICRO_MINIATURE
READ_ACCEL2_TEST: TEST_POINTMICRO_MINIATURE; MICRO_MINIATURE
READ_BRAKE1_TEST, READ_BRAKE2_TEST: TEST_POINTMICRO_MINIATURE; MICRO_MINIATURE
SIGNAL_ACCEL1_TEST: 12V_TEST; MICRO_MINIATURE
SIGNAL_ACCEL2_TEST: TEST_POINTMICRO_MINIATURE; MICRO_MINIATURE
SIGNAL_BRAKE1_TEST, SIGNAL_BRAKE2_TEST: TEST_POINTMICRO_MINIATURE; MICRO_MINIATURE
SIGNAL_GND: TEST_POINTMICRO_MINIATURE; MICRO_MINIATURE
U5: TEENSY_3.2_SIMPLE
U10, U23: LM293DG4; SOIC-08
U34: TXB0104TSSOP; TSSOP-14
U37: MCP3204; SO14
U38, U39, U44, U45: MAX7480; SOIC-08
U46: TEST_POINTMICRO_MINIATURE; MICRO_MINIATURE
U100, U101: MCP6002SOIC; SOIC-08

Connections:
3V_MAIN_TEENSY: R42.2, U5.3.3V, U34.8 (OE)
+3V3: C12.2, C19.2, C28.2, R116.2, U10.8 (VDD), U23.8 (VDD), U34.1 (VCCA); also elsewhere on the board
+5V: BR1.2, BR2.2, C3.2, C4.2, C25.2, C35.2, C36.2, C39.1, C44.1, C47.1, C49.1, C101.1, C102.1, C106.1, C107.1, C117.2, C118.2, CAN100.3, PU1.2, PU2.2, U5.VIN, U34.14 (VCCB), U37.13 (VREF), U37.14 (VDD), U38.4 (VDD), U38.7 (!SHDN), U39.4 (VDD), U39.7 (!SHDN), U44.4 (VDD), U44.7 (!SHDN), U45.4 (VDD), U45.7 (!SHDN), U100.8 (VDD), U101.8 (VDD); also elsewhere on the board
ACCEL1_BUFF: ACCEL2_BUFF_TEST.P$1, U45.2 (IN), U100.6 (VINB-), U100.7 (VOUTB)
ACCEL2_BUFF: ACCEL1_BUFF_TEST.P$1, U44.2 (IN), U100.1 (VOUTA), U100.2 (VINA-)
BMS_OK: D6.A; also elsewhere on the board
BMS_OK_READ: R25.2, R133.1, U5.A5
BRAKE1_BUFF: BRAKE2_BUFF_TEST.P$1, U39.2 (IN), U101.6 (VINB-), U101.7 (VOUTB)
BRAKE2_BUFF: BRAKE1_BUFF_TEST.P$1, U38.2 (IN), U101.1 (VOUTA), U101.2 (VINA-)
BRAKE_LIGHT_CTRL: U5.D0(RX1); also elsewhere on the board
BSPD_OK: D7.A; also elsewhere on the board
BSPD_OK_READ: R26.2, R132.1, U5.A6
CANH: CAN100.7; also elsewhere on the board
CANL: CAN100.6; also elsewhere on the board
CS1_5V: U34.13 (B1), U37.8 (!CS!/SHDN)
CS1_TEENSY: U5.D10(TX2), U34.2 (A1)
FAN1CONTROL: U5.D5; also elsewhere on the board
FAN2CONTROL: U5.D6; also elsewhere on the board
GND: C3.1, C4.1, C12.1, C19.1, C25.1, C28.1, C35.1, C36.1, C37.1, C38.2, C39.2, C42.1, C43.2, C44.2, C45.2, C46.2, C47.2, C48.1, C49.2, C50.1, C101.2, C102.2, C106.2, C107.2, C117.1, C118.1, CAN100.2, CAN100.8, PD1.2, PD2.2, R42.1, R105.1, R106.1, R107.1, R112.1, R117.1, R131.2, R132.2, R133.2, R134.2, R135.2, R136.2, R137.2, R138.2, SIGNAL_GND.P$1, U5.GND, U10.4 (VSS), U23.4 (VSS), U34.7 (GND), U37.7 (DGND), U37.12 (AGND), U38.3 (GND), U39.3 (GND), U44.3 (GND), U45.3 (GND), U46.P$1, U100.4 (VSS), U101.4 (VSS); also elsewhere on the board
INVERTER_CTRL: U5.D9(RX2); also elsewhere on the board
MISO_5V: U34.11 (B3), U37.10 (DOUT)
MISO_TEENSY: U5.D12, U34.4 (A3)
MOSI_5V: U34.12 (B2), U37.9 (DIN)
MOSI_TEENSY: U5.D11, U34.3 (A2)
unnamed: C43.1, U39.8 (CLK)
unnamed: C42.2, U39.1 (COM), U39.6 (OS)
unnamed: D4.C, R23.1
unnamed: D8.C, R27.1
unnamed: D5.C, R24.1
unnamed: D6.C, R25.1
unnamed: D3.C, R22.1
unnamed: D1.C, R20.1
unnamed: D2.C, R21.1
unnamed: D7.C, R26.1
unnamed: C45.1, U44.8 (CLK)
unnamed: C46.1, U45.8 (CLK)
unnamed: C48.2, U44.1 (COM), U44.6 (OS)
unnamed: C38.1, U38.8 (CLK)
unnamed: C37.2, U38.1 (COM), U38.6 (OS)
unnamed: C50.2, U45.1 (COM), U45.6 (OS)
OKHS: D5.A; also elsewhere on the board
OKHS_READ: R24.2, R134.1, U5.A4
READ_ACCEL1: READ_ACCEL2_TEST.P$1, U37.3 (CH2), U45.5 (OUT)
READ_ACCEL2: READ_ACCEL1_TEST.P$1, U37.4 (CH3), U44.5 (OUT)
READ_BRAKE1: READ_BRAKE2_TEST.P$1, U37.2 (CH1), U39.5 (OUT)
READ_BRAKE2: READ_BRAKE1_TEST.P$1, U37.1 (CH0), U38.5 (OUT)
RX_MAIN: CAN100.4, U5.D4(CANRX)
SCK_5V: U34.10 (B4), U37.11 (CLK)
SCK_TEENSY: U5.D13, U34.5 (A4)
SHUTDOWN_B: D1.A; also elsewhere on the board
SHUTDOWN_B_READ: R20.2, R138.1, U5.A0
SHUTDOWN_C: D2.A; also elsewhere on the board
SHUTDOWN_C_READ: R21.2, R137.1, U5.A1
SHUTDOWN_D: D3.A; also elsewhere on the board
SHUTDOWN_D_READ: R22.2, R136.1, U5.A2
SHUTDOWN_E: D4.A; also elsewhere on the board
SHUTDOWN_E_READ: R23.2, R135.1, U5.A3
SIGNAL_ACCEL1: PD1.1, PU1.1, SIGNAL_ACCEL2_TEST.P$1, U100.5 (VINB+); also elsewhere on the board
SIGNAL_ACCEL2: PD2.1, PU2.1, SIGNAL_ACCEL1_TEST.P$1, U100.3 (VINA+); also elsewhere on the board
SIGNAL_BRAKE1: BR1.1, SIGNAL_BRAKE2_TEST.P$1, U101.5 (VINB+); also elsewhere on the board
SIGNAL_BRAKE2: BR2.1, SIGNAL_BRAKE1_TEST.P$1, U101.3 (VINA+); also elsewhere on the board
SOFTWARE_OK: D8.A; also elsewhere on the board
SOFTWARE_OK_READ: R27.2, R131.1, U5.A7
TEENSY_OK: U5.A9; also elsewhere on the board
TX_MAIN: CAN100.1, U5.D3(CANTX)
WATCHDOG_IN: U5.A8; also elsewhere on the board
WHEELSPEED_DIV: R116.1, R117.2, U10.2 (VINA-), U10.6 (VINB-), U23.2 (VINA-), U23.6 (VINB-)
WS1_IN: R107.2, U10.5 (VINB+); also elsewhere on the board
WS1_READ: U5.D7(RX3), U10.7 (VOUTB)
WS2_IN: R112.2, U10.3 (VINA+); also elsewhere on the board
WS2_READ: U5.D8(TX3), U10.1 (VOUTA)
WS3_IN: R106.2, U23.3 (VINA+); also elsewhere on the board
WS3_READ: U5.D1(TX1), U23.1 (VOUTA)
WS4_IN: R105.2, U23.5 (VINB+); also elsewhere on the board
WS4_READ: U5.D2, U23.7 (VOUTB)

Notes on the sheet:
Pullup/down resistors to detect open circuit. Install only one per signal on ACCEL1 and ACCEL2.
470pF for ~1kHz filter (1.13kHz)
Ethan Weinstock
Main microcontroller and analog signals circuitry.
Place note on PCB
Using Teensy 3.3V as enable signal
680 Hz max
don't need resistor between ADC and TXB MCP has a rise time of 100 ns slew rate of 0.05 V/ns the capacitance is 10 pF with a via -> current of 0.05 mA since we have no via the current is less (based on ADI staying well grounded)

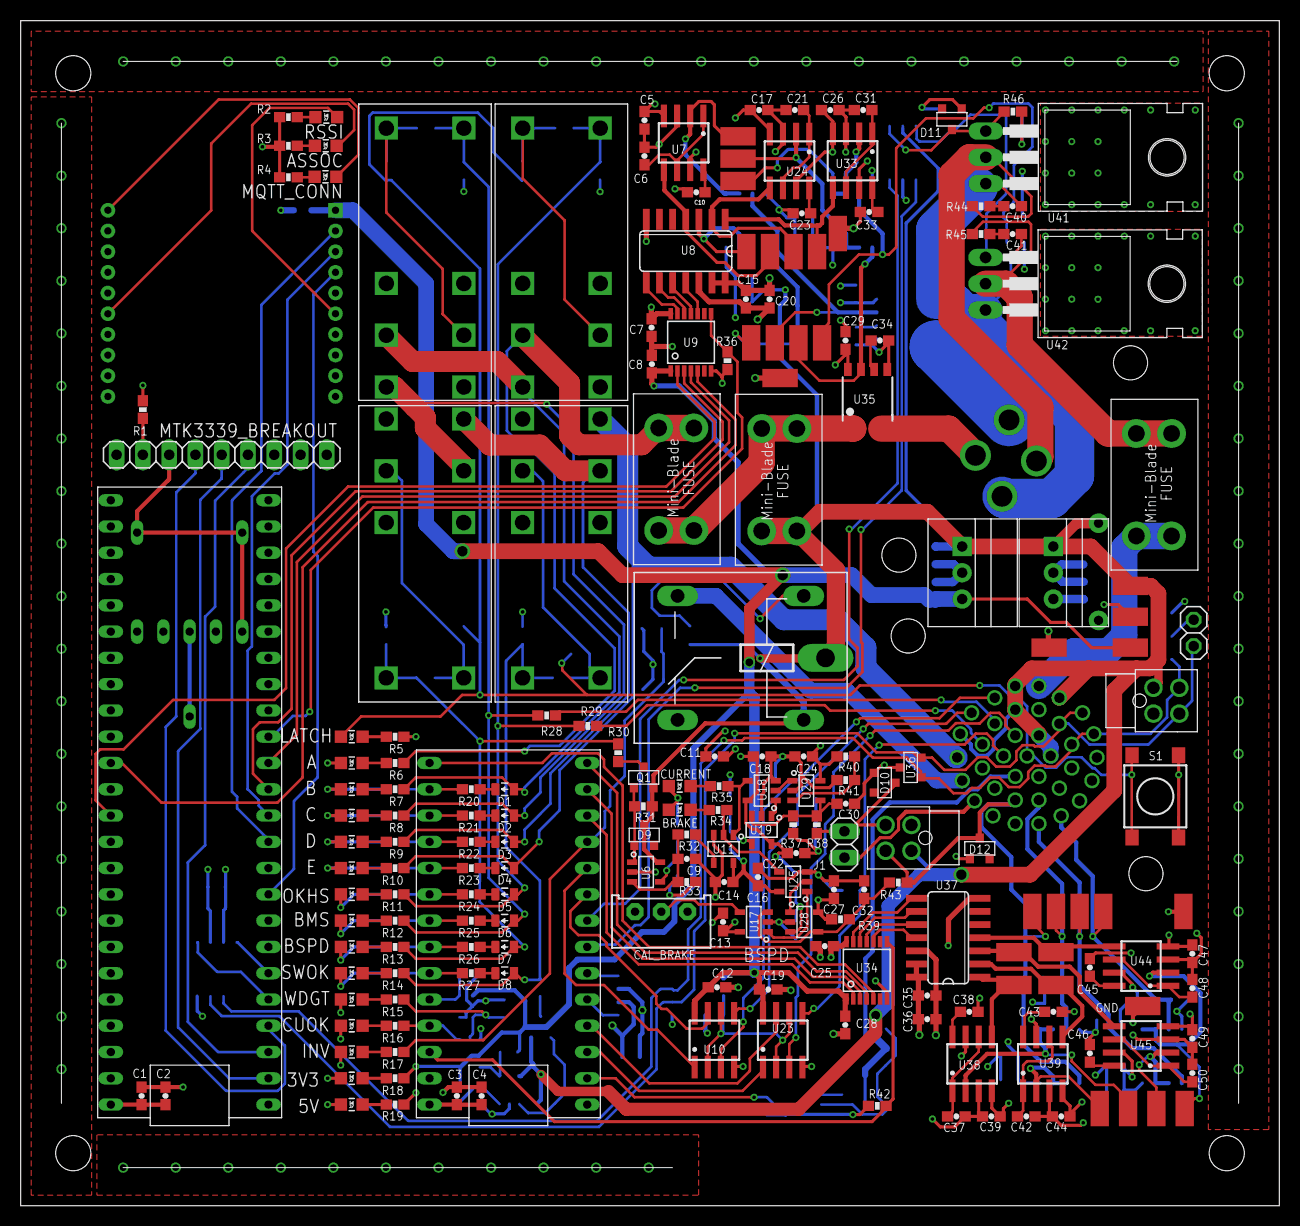
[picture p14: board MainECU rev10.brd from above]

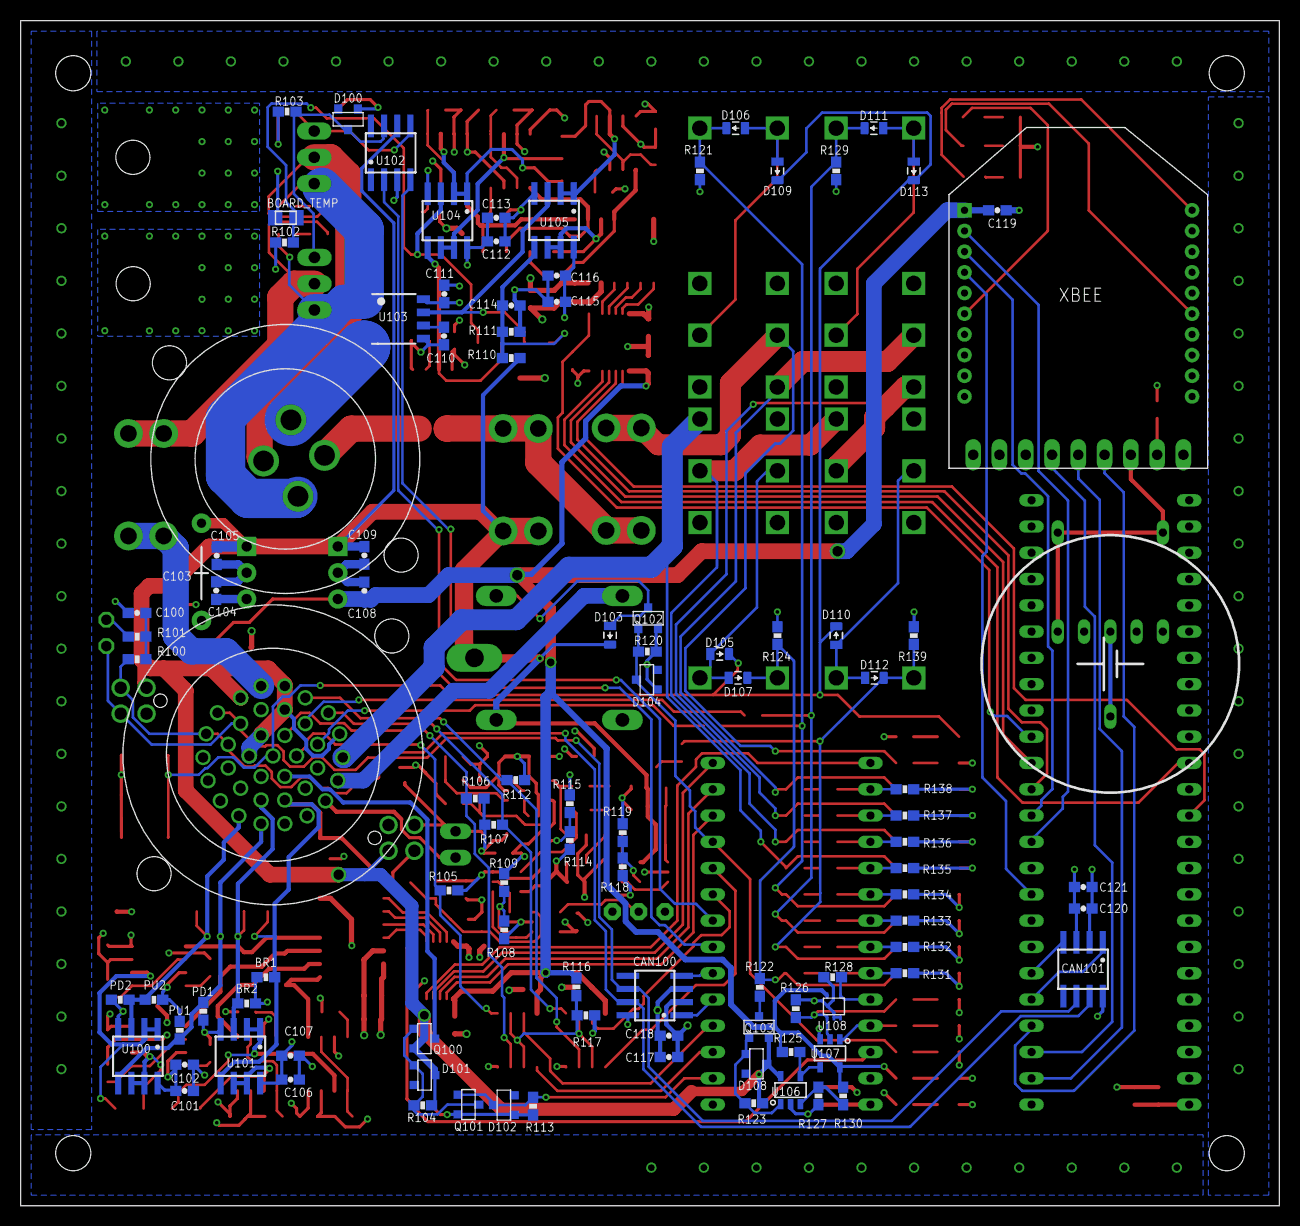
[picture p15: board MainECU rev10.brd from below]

Board: 4 copper layers, 121.7 x 114.6 mm, 310 parts (102 on the bottom side), 186 nets.

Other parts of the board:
U$1, U$2, U$3, U$4: M3_MOUNTING

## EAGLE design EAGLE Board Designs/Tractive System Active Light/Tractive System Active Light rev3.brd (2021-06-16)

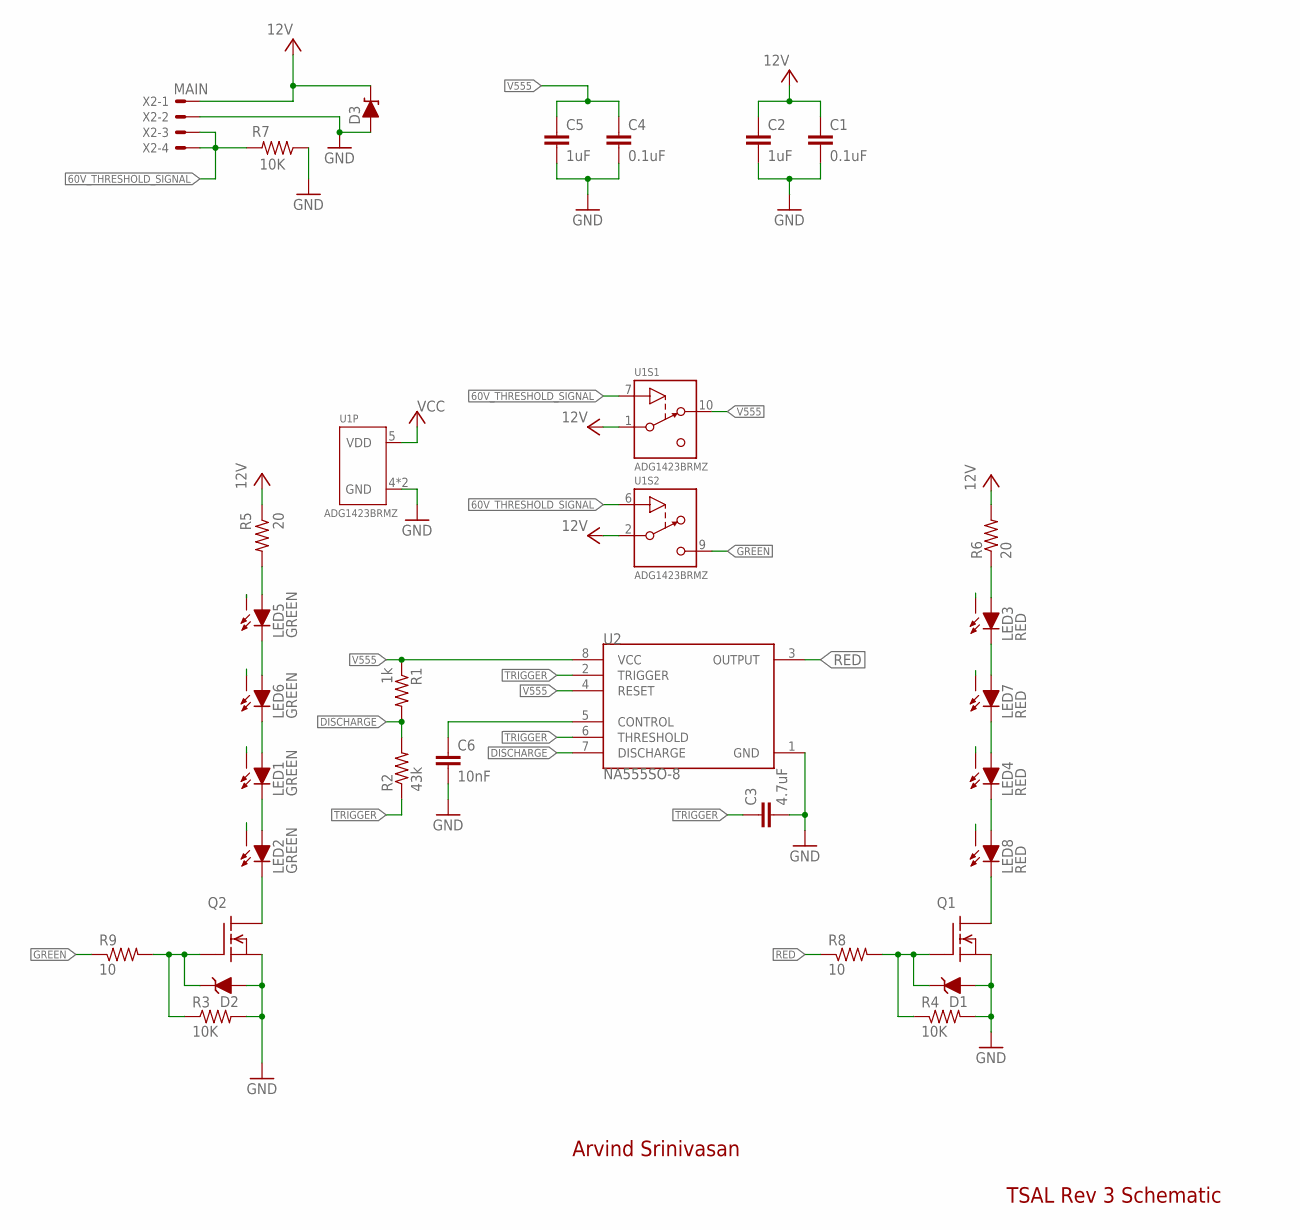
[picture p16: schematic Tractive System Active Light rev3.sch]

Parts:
C1, C4: 0.1uF; 0603-CAP; TOLERANCE 5%; VOLTAGE 25V
C2, C5: 1uF; 0603-CAP; TOLERANCE 5%; VOLTAGE 25V
C3: 4.7uF; 0603-CAP; TOLERANCE 5%; VOLTAGE 25V
C6: 10nF; 0603-CAP; TOLERANCE 5%; VOLTAGE 25V
D1, D2: MMBZ5246BLT1G; SOT23
D3: D15V0S1U2LP1608; U-DFN1608-2
LED1, LED2, LED5, LED6: GREEN; XP-E2
LED3, LED4, LED7, LED8: RED; XP-E2
Q1, Q2: DMG3406LSOT; SOT23
R1: 1k; 0603-RES; TOLERANCE 1%
R2: 43k; 0603-RES; TOLERANCE 1%
R3, R4, R7: 10K; 0603-RES; TOLERANCE 1%
R5, R6: 20; 0603-RES; TOLERANCE 1%
R8, R9: 10; 0603-RES; TOLERANCE 1%
U1: ADG1423; MSOP-10
U2: NA555SO-8; SOIC-08
X2: MAIN; NANO-FIT_RIGHT_ANGLE-4-SURFACE

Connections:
60V_THRESHOLD_SIGNAL: R7.2, U1.6 (IN), U1.7 (IN), X2.3, X2.4
DISCHARGE: R1.2, R2.2, U2.7 (DISCHARGE)
GND: C1.2, C2.2, C3.2, C4.2, C5.2, C6.2, D1.1 (A), D2.1 (A), D3.P$1 (A), Q1.2 (S), Q2.2 (S), R3.2, R4.2, R7.1, U1.4 (GND), U1.8 (GND), U2.1 (GND), X2.2
GREEN: R9.1, U1.9 (D)
unnamed: LED1.A, LED6.C
unnamed: LED2.C, Q2.3 (D)
unnamed: LED5.C, LED6.A
unnamed: D1.3 (C), Q1.1 (G), R4.1, R8.2
unnamed: LED5.A, R5.2
unnamed: D2.3 (C), Q2.1 (G), R3.1, R9.2
unnamed: LED8.C, Q1.3 (D)
unnamed: LED3.A, R6.1
unnamed: C6.1, U2.5 (CONTROL)
unnamed: LED1.C, LED2.A
unnamed: LED3.C, LED7.A
unnamed: LED4.A, LED7.C
unnamed: LED4.C, LED8.A
RED: R8.1, U2.3 (OUTPUT)
THERM: LED1.X, LED2.X, LED3.X, LED4.X, LED5.X, LED6.X, LED7.X, LED8.X
TRIGGER: C3.1, R2.1, U2.2 (TRIGGER), U2.6 (THRESHOLD)
V555: C4.1, C5.1, R1.1, U1.10 (D), U2.4 (RESET), U2.8 (VCC)
VCC: C1.1, C2.1, D3.P$2 (C), R5.1, R6.2, U1.1 (S), U1.2 (S), U1.5 (VDD), X2.1

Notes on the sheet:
Arvind Srinivasan
TSAL Rev 3 Schematic

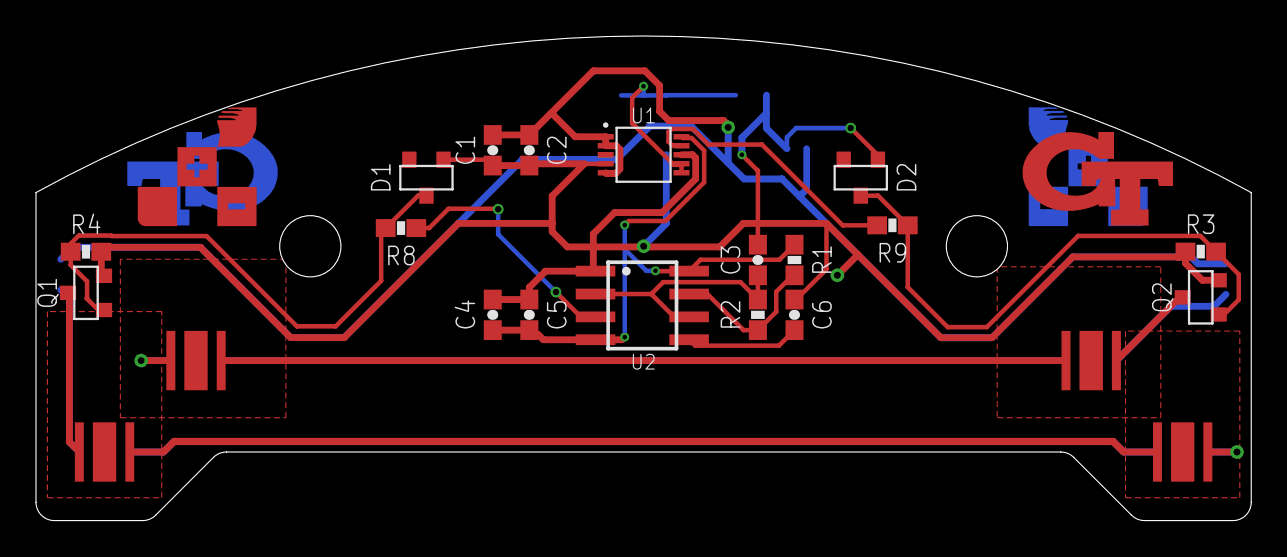
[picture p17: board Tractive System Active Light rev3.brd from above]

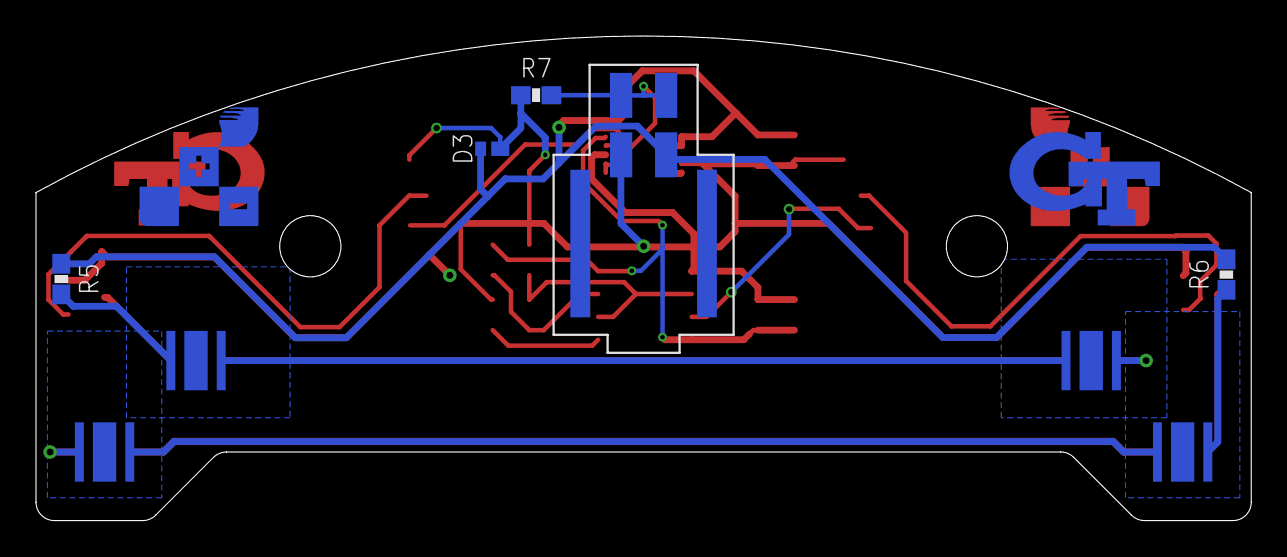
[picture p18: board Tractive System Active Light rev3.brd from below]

Board: 2 copper layers, 67.5 x 26.9 mm, 33 parts (9 on the bottom side), 22 nets.

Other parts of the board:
$$U$1: M3_MOUNTING
U$2: M3_MOUNTING

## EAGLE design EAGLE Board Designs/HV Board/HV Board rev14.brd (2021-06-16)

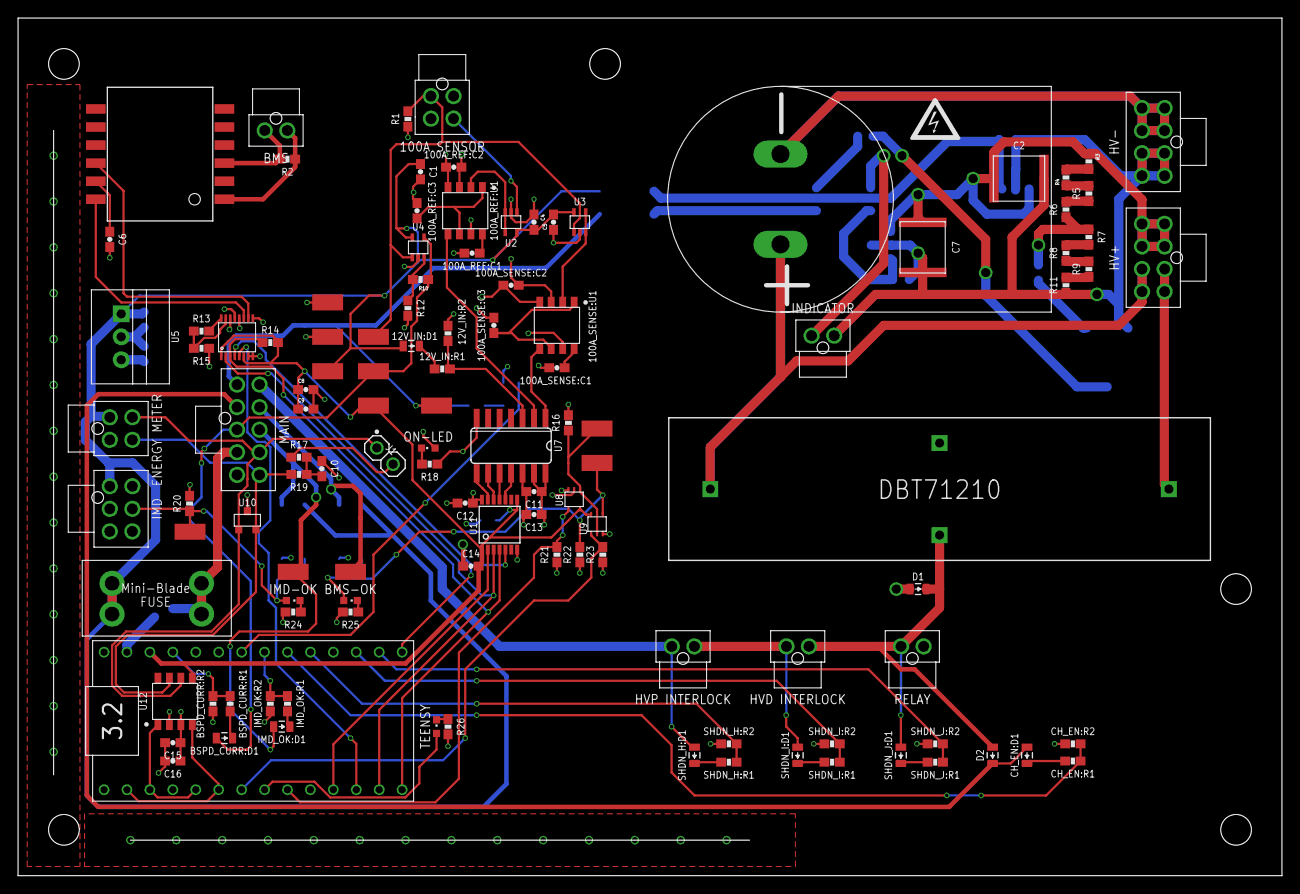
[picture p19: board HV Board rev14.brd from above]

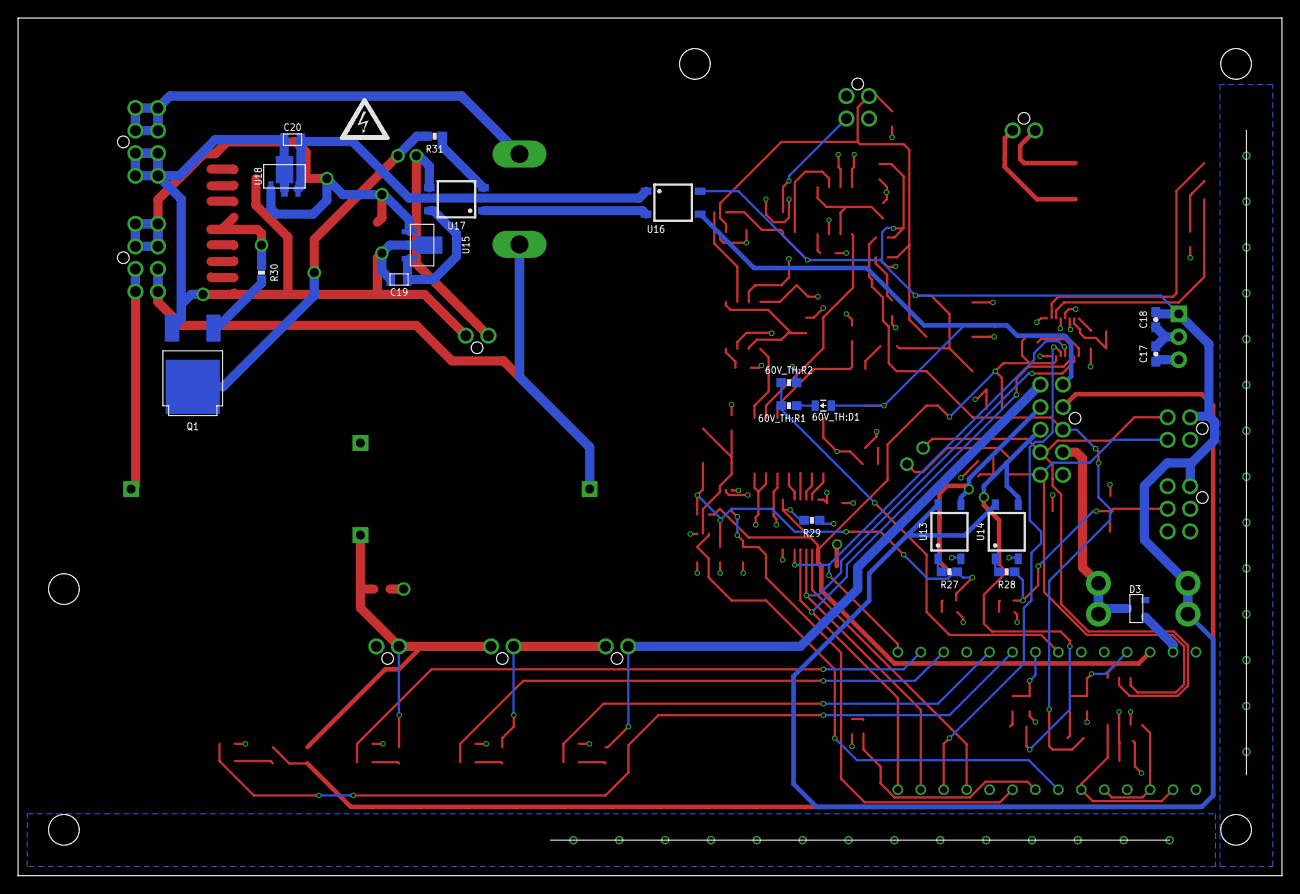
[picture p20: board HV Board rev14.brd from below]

Board: 4 copper layers, 140.0 x 95.0 mm, 143 parts (21 on the bottom side), 93 nets.

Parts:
12V_IN:D1, 60V_TH:D1: TS4148 RYG; 0805_D
12V_IN:R1, 60V_TH:R1: 12K; 0603-RES@1
12V_IN:R2, 60V_TH:R2: 43K; 0603-RES@1
100A_REF:C1, 100A_SENSE:C1: 680pF; 0603-CAP@1
100A_REF:C2, 100A_REF:C3, 100A_SENSE:C2, 100A_SENSE:C3: 0.1uF; 0603-CAP@1
100A_REF:U1, 100A_SENSE:U1: MAX7480; SOIC-08@2
$$$$U$3: DBT71210
$$U$1, $$U$2: M3_MOUNTING
$$U$3, $$U$12: TEST_POINTMICRO_MINIATURE; MICRO_MINIATURE
BMS-OK: GREEN; LED-603
BOARDFUSE: 2A; MINI-BLADE_FUSE_HOLDER
BSPD_CURR:D1: TS4148 RYG; 0805_D
BSPD_CURR:R1: 12K; 0603-RES@1
BSPD_CURR:R2: 43K; 0603-RES@1
C1, C4, C5, C9, C11, C12, C14, C15: 0.1uF; 0603-CAP@1
C2, C7: CAPACITOR_2220_630V_1UF; 2220-CAP
C3: 180uF; LLS2V181MELA
C6: 27pF; 0603-CAP@1
C8, C13, C16: 1uF; 0603-CAP@1
C10: 4.7nF; 0603-CAP@1
C17, C18: 10uF; 0603-CAP@1
C19, C20: CAPACITOR_0805_25V_22UF; 0805-CAP
CH_EN:D1: TS4148 RYG; 0805_D
CH_EN:R1: 12K; 0603-RES@1
CH_EN:R2: 43K; 0603-RES@1
CURRENT1: 100A SENSOR; NANO-FIT_VERTICAL-4
D1, D2: TS4148 RYG; 0805_D
D3: TVS_15V; SOT-23
ENERGYMETER: ENERGY METER; NANO-FIT_VERTICAL-4
HV+: CONNECTOR-8_NF_T_V_NATURAL; MOLEX_NANOFIT_PTH_08
HV-: CONNECTOR-8_NF_T_V_BLACK; MOLEX_NANOFIT_PTH_08
IMD: IMD; NANO-FIT_VERTICAL-6
IMD-OK: YELLOW; LED-603
IMD_OK:D1: TS4148 RYG; 0805_D
IMD_OK:R1: 12K; 0603-RES@1
IMD_OK:R2: 43K; 0603-RES@1
INDICATOR: INDICATOR; NANO-FIT_VERTICAL-2
INTERLOCK1: HVP INTERLOCK; NANO-FIT_VERTICAL-2
INTERLOCK2: HVD INTERLOCK; NANO-FIT_VERTICAL-2
ISOSPI: BMS; NANO-FIT_VERTICAL-2
J1: JUMPER.1; 1X02
MAIN: MAIN; NANO-FIT_VERTICAL-10
ON-LED: BLUE; LED-603
Q1: TRANSISTOR_N_MOS_2-7K1S_TK6P65W; DPAK(2-7K1S)
R1, R21: 10K; 0603-RES@1
R2: 100; 0603-RES@1
R3, R4, R5, R6: 162k; 0603-RES@1
R7, R8, R9, R11, R16, R20, R22, R23, R29: 10k; 0603-RES@1
R10: 1.4k; 0603-RES@1
R12, R13, R15, R26: 1k; 0603-RES@1
R14: 2k; 0603-RES@1
R17, R19: 60; 0603-RES@1
R18, R24, R25: 1K; 0603-RES@1
R27: 360; 0603-RES@1
R28: 4.7k; 0603-RES@1
R30: 10; 0603-RES@1
R31: 5k; 0603-RES@1
RELAY: RELAY; NANO-FIT_VERTICAL-2
SHDN_H:D1: TS4148 RYG; 0805_D
SHDN_H:R1: 12K; 0603-RES@1
SHDN_H:R2: 43K; 0603-RES@1
SHDN_I:D1: TS4148 RYG; 0805_D
SHDN_I:R1: 12K; 0603-RES@1
SHDN_I:R2: 43K; 0603-RES@1
SHDN_J:D1: TS4148 RYG; 0805_D
SHDN_J:R1: 12K; 0603-RES@1
SHDN_J:R2: 43K; 0603-RES@1
TEENSY: RED; LED-603
TEENSY3.1: TEENSY_3.2_SIMPLE
U1: HM2102NLT
U2, U3, U4: OPAMP_1_CHANNEL_OPA991; SC-70-5
U5: OKI-78SR-5; OKI-78SR@1
U6: LTC6820; MSOP-16
U7: MCP3204; SO14
U8: STWD100PYW83F; SOT323-5
U9: SN74LVC1G08; SOT323-5
U10: CDSOT23-T24CAN-Q; SOT23
U11: TXB0104TSSOP; TSSOP-14
U12: CAN_TRANSCIEVER_TCAN1051HQV-Q1; SOIC-08
U13, U14, U16, U17: CPC1002N; SOP04
U15, U18: VOLTAGE_REGULATOR_SOT89_12V; SOT89
U$3, U$4, U$5, U$6, U$7, U$8, U$9, U$10, U$11, U$13: TEST_POINTMICRO_MINIATURE; MICRO_MINIATURE
U$14, U$15, U$16: M3_MOUNTING
U$17, U$19: HV_0.50"

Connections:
12V_IN:INPUT_POST_DIODE: 12V_IN:D1.C, 12V_IN:R1.1
60V_TH:INPUT_POST_DIODE: 60V_TH:D1.C, 60V_TH:R1.1
60V_THRESHOLD_SIGNAL: 60V_TH:D1.A, MAIN.P$1, U16.3, U$8.P$1
60V_THRESHOLD_TEENSY: 60V_TH:R1.2, 60V_TH:R2.1, TEENSY3.1.A6
100A_REF: CURRENT1.P$3, U2.1
100A_REF:CLK: 100A_REF:C1.1, 100A_REF:U1.8
100A_REF:COM: 100A_REF:C3.1, 100A_REF:U1.1, 100A_REF:U1.6
100A_REF_BUFF: 100A_REF:U1.2, U2.3, U2.4
100A_REF_FILT: 100A_REF:U1.5, U7.2
100A_SENSE: CURRENT1.P$2, R1.1, U3.1, U4.1, U$4.P$1
100A_SENSE:CLK: 100A_SENSE:C1.1, 100A_SENSE:U1.8
100A_SENSE:COM: 100A_SENSE:C3.1, 100A_SENSE:U1.1, 100A_SENSE:U1.6
100A_SENSE_BUFF: 100A_SENSE:U1.2, U3.3, U3.4
100A_SENSE_FILT: 100A_SENSE:U1.5, U7.1
+3V3: C8.1, C9.1, C14.1, R14.1, R29.1, TEENSY3.1.3.3V, U6.1, U6.6, U8.5, U9.5, U11.1, U11.8, U12.5, U$7.P$1
+5V: 100A_REF:C2.1, 100A_REF:U1.4, 100A_REF:U1.7, 100A_SENSE:C2.1, 100A_SENSE:U1.4, 100A_SENSE:U1.7, $$U$3.P$1, C11.1, C12.1, C13.1, C15.2, C16.2, C17.1, CURRENT1.P$1, ON-LED.A, TEENSY3.1.VIN, U5.3, U6.7, U6.8, U6.9, U6.12, U7.13, U7.14, U11.14, U12.3
+12V: 12V_IN:D1.A, BOARDFUSE.R1, BOARDFUSE.R2, C1.2, C4.2, C5.2, C18.1, ENERGYMETER.P$1, IMD.P$1, U2.5, U3.5, U4.5, U5.1, U13.4, U14.4, U16.4, U$5.P$1
+12VIN: BOARDFUSE.L1, BOARDFUSE.L2, D3.3, MAIN.P$4
+12V_SCALED_3.3V: 12V_IN:R1.2, 12V_IN:R2.1, U7.3
BMS_OK: MAIN.P$7, U13.3, U$13.P$1
BMS_OK_3.3V: BMS-OK.A, R22.2, R27.1, U9.4, U$10.P$1
BMS_STATUS: R23.2, TEENSY3.1.D5, U9.1
BSPD_CURR:INPUT_POST_DIODE: BSPD_CURR:D1.C, BSPD_CURR:R1.1
BSPD_CURRENT: BSPD_CURR:D1.A, MAIN.P$3, R10.1, U4.4, U$6.P$1
BSPD_CURR_TEENSY: BSPD_CURR:R1.2, BSPD_CURR:R2.1, TEENSY3.1.A9
CANH: ENERGYMETER.P$4, MAIN.P$10, R19.2, U10.2, U12.7
CANL: ENERGYMETER.P$3, J1.1, MAIN.P$9, U10.1, U12.6
CANRX: TEENSY3.1.D0(RX1), TEENSY3.1.D4(CANRX), U12.4
CANTX: TEENSY3.1.D1(TX1), TEENSY3.1.D3(CANTX), U12.1
CHARGE_ENABLE: CH_EN:D1.A, D2.C, MAIN.P$2
CHARGE_ENABLE_TEENSY: CH_EN:R1.2, CH_EN:R2.1, TEENSY3.1.A4
CH_EN:INPUT_POST_DIODE: CH_EN:D1.C, CH_EN:R1.1
CS_ADC_5V: U7.8, U11.13
CS_ADC_TEENSY: TEENSY3.1.D9(RX2), U11.2
CS_LTC6820: TEENSY3.1.D10(TX2), U6.5
DISCHARGE+: $$$$U$3.CONTACT2, HV+.1, HV+.2
GND: 12V_IN:R2.2, 60V_TH:R2.2, 100A_REF:C1.2, 100A_REF:C2.2, 100A_REF:C3.2, 100A_REF:U1.3, 100A_SENSE:C1.2, 100A_SENSE:C2.2, 100A_SENSE:C3.2, 100A_SENSE:U1.3, $$$$U$3.COIL+, BSPD_CURR:R2.2, C1.1, C4.1, C5.1, C6.2, C8.2, C9.2, C10.1, C11.2, C12.2, C13.2, C14.2, C15.1, C16.1, C17.2, C18.2, CH_EN:R2.2, CURRENT1.P$4, D1.A, D3.1, ENERGYMETER.P$2, IMD.P$2, IMD.P$3, IMD.P$4, IMD_OK:R2.2, MAIN.P$5, R1.2, R12.2, R15.2, R16.1, R18.2, R20.2, R21.2, R22.1, R23.1, R24.2, R25.2, R26.2, R29.2, RELAY.P$2, SHDN_H:R2.2, SHDN_I:R2.2, SHDN_J:R2.2, TEENSY3.1.AGND, TEENSY3.1.GND, U2.2, U3.2, U4.2, U5.2, U6.13, U6.14, U7.7, U7.12, U8.2, U8.3, U9.3, U10.3, U11.7, U12.2, U13.2, U14.2, U$3.P$1
HV+FUSED: C2.1, C7.1, HV+.3, HV+.4, HV+.7, HV+.8, R3.1, U15.1, U18.1
HV+UNFUSED: $$$$U$3.CONTACT1, C3.P$1, HV+.5, HV+.6
HV-FUSED: C2.2, C7.2, C19.2, C20.2, HV-.1, HV-.2, HV-.5, HV-.6, INDICATOR.P$2, Q1.3, R11.2, U15.2, U15.2@2, U18.2, U18.2@2
HV-UNFUSED: C3.P$2, HV-.3, HV-.4, HV-.7, HV-.8
IM: U1.P$10, U6.10
IMD_OK: $$U$12.P$1, IMD_OK:D1.A, MAIN.P$8, U14.3
IMD_OK:INPUT_POST_DIODE: IMD_OK:D1.C, IMD_OK:R1.1
IMD_OK_12V: IMD.P$5, IMD-OK.A, R20.1, R28.1, U$11.P$1
IMD_OK_TEENSY: IMD_OK:R1.2, IMD_OK:R2.1, TEENSY3.1.A5
IP: U1.P$12, U6.11
ISOSPI-M: ISOSPI.P$2, R2.2, U1.P$3
ISOSPI-P: ISOSPI.P$1, R2.1, U1.P$1
MISO_5V: U7.10, U11.11
MISO_TEENSY: R14.2, TEENSY3.1.D12, U6.3, U11.4
MOSI_5V: U7.9, U11.12
MOSI_TEENSY: TEENSY3.1.D11, U6.2, U11.3
unnamed: ON-LED.C, R18.1
unnamed: Q1.1, R30.2
unnamed: C19.1, U15.3, U17.4
unnamed: R9.1, R11.1
unnamed: R28.2, U14.1
unnamed: IMD-OK.C, R24.1
unnamed: R8.2, R9.2
unnamed: C10.2, R17.1, R19.1
unnamed: R7.1, R8.1
unnamed: R10.2, R12.1, U4.3
unnamed: R27.2, U13.1
unnamed: BMS-OK.C, R25.1
unnamed: C20.1, U16.1, U18.3
unnamed: R6.1, R7.2, R30.1
unnamed: R5.2, R6.2
unnamed: R4.1, R5.1
unnamed: R3.2, R4.2
unnamed: J1.2, R17.2
unnamed: R26.1, TEENSY.C
unnamed: R31.1, U17.2
unnamed: R13.1, U6.16
unnamed: R13.2, R15.1, U6.15
unnamed: U16.2, U17.1
unnamed: INDICATOR.P$1, U17.3
unnamed: C6.1, U1.P$11
unnamed: Q1.2, R31.2
SCK_5V: U7.11, U11.10
SCK_TEENSY: TEENSY3.1.D13, U6.4, U11.5
SHDN_H:INPUT_POST_DIODE: SHDN_H:D1.C, SHDN_H:R1.1
SHDN_I:INPUT_POST_DIODE: SHDN_I:D1.C, SHDN_I:R1.1
SHDN_J:INPUT_POST_DIODE: SHDN_J:D1.C, SHDN_J:R1.1
SHUTDOWN_H: INTERLOCK1.P$1, MAIN.P$6, SHDN_H:D1.A
SHUTDOWN_H_TEENSY: SHDN_H:R1.2, SHDN_H:R2.1, TEENSY3.1.A3
SHUTDOWN_I: INTERLOCK1.P$2, INTERLOCK2.P$1, SHDN_I:D1.A
SHUTDOWN_I_TEENSY: SHDN_I:R1.2, SHDN_I:R2.1, TEENSY3.1.A1
SHUTDOWN_J: $$$$U$3.COIL-, D1.C, D2.A, INTERLOCK2.P$2, RELAY.P$1, SHDN_J:D1.A
SHUTDOWN_J_TEENSY: SHDN_J:R1.2, SHDN_J:R2.1, TEENSY3.1.A0
TEENSY_STATUS: TEENSY.A, TEENSY3.1.D6
WATCHDOG_INPUT: R21.1, TEENSY3.1.D7(RX3), U8.4
WATCHDOG_OK: R16.2, U8.1, U9.2, U$9.P$1

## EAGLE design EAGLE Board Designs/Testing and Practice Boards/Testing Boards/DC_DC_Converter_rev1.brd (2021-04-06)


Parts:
C1: 4.7 mF; EKYC*MM
C2: LGG2G181MELA25; L*A
F1: FUSE_MINIBLADE; MINI-BLADE_FUSE_HOLDER
F2, F3: 885_FUSE; 0885
J1, J2: CONNECTOR-2; MOLEX_NANOFIT_PTH_02
J3: CONNECTOR-4MINIFIT; MOLEX_MINIFIT_PTH_04
U1: DCM3714BD2K13E0C09; 3714DCM_VIA

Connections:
12V_UNFUSED: C1.+ (PLUS), F1.L1 (1), F1.L2 (1), U1.3 (OUT+), U1.9 (SENSE+)
+12V: F1.R1 (2), F1.R2 (2), J3.1, J3.2
GND: C1.- (MINUS), J3.3, J3.4, U1.4 (OUT-), U1.8 (SENSE-)
HV+: F2.1, J1.1, J1.2
HV-: F3.1, J2.1, J2.2
IN+: C2.+ (PLUS), F2.2, U1.1 (IN+)
IN-: C2.- (MINUS), F3.2, U1.2 (IN-)
VDDE: U1.5 (VDDE)

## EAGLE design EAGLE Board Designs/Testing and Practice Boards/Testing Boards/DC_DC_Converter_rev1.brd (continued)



Board: 2 copper layers, 99.9 x 58.7 mm, 17 parts (4 on the bottom side), 7 nets.

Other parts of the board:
U$1, U$2, U$3, U$8, U$9, U$10: HV_0.50"
U$6: LOGO_HYTECH_1.0"
U$7: LOGO_GT_0.50"

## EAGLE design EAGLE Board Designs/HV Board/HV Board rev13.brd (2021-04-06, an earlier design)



Board: 4 copper layers, 140.0 x 95.0 mm, 161 parts (27 on the bottom side), 104 nets.

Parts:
60V-THRESHOLD:D1: TS4148 RYG; 0805_D
60V-THRESHOLD:R1: 12k; 0603-RES
60V-THRESHOLD:R2: 10k; 0603-RES
100A_REF:C1, 100A_SENSE:C1, 300A_REF:C1, 300A_SENSE:C1: 530pF; 0603-CAP
100A_REF:C2, 100A_REF:C3, 100A_SENSE:C2, 100A_SENSE:C3, 300A_REF:C2, 300A_REF:C3, 300A_SENSE:C2, 300A_SENSE:C3: 0.1uF; 0603-CAP
100A_REF:U1, 100A_SENSE:U1, 300A_REF:U1, 300A_SENSE:U1: MAX7480; SOIC-08
$$U$1, $$U$2: M3_MOUNTING
$$U$12: DBT71210
BMS-OK: GREEN; LED-603
BOARDFUSE: 2A; MINI-BLADE_FUSE_HOLDER
BSPD_CURR:D1: TS4148 RYG; 0805_D
BSPD_CURR:R1: 12K; 0603-RES
BSPD_CURR:R2: 43K; 0603-RES
C1: 180uF; LLS2V181MELA
C2, C5, C6, C8, C9, C10, C11: 0.1uF; 0603-CAP
C3: 27pF; 0603-CAP
C4: 4.7nF; 0603-CAP
C7, C12: 1uF; 0603-CAP
C13, C14: 10uF; 0603-CAP
CHARGE_ENABLE:D1: TS4148 RYG; 0805_D
CHARGE_ENABLE:R1: 12K; 0603-RES
CHARGE_ENABLE:R2: 43K; 0603-RES
CURRENT1: 100A SENSOR; NANO-FIT_VERTICAL-4
CURRENT2: 300A SENSOR; NANO-FIT_VERTICAL-4
D1, D2, D3: TS4148 RYG; 0805_D
D4: MMBZ5246BLT1G; SOT23
D5: TVS_DIODE; U-DFN1608-2
DISCHARGE+: DISCHARGE+; NANO-FIT_VERTICAL-2
DISCHARGE-: DISCHARGE-; NANO-FIT_VERTICAL-2
ENERGYMETER: ENERGY METER; NANO-FIT_VERTICAL-4
HV+FUSED: HV+FUSED; NANO-FIT_VERTICAL-2
HV+UNFUSED: HV+UNFUSED; NANO-FIT_VERTICAL-2
HV-FUSED: HV-FUSED; NANO-FIT_VERTICAL-2
HV-UNFUSED: HV-UNFUSED; NANO-FIT_VERTICAL-2
IMD: IMD; NANO-FIT_VERTICAL-6
IMD+: IMD+; NANO-FIT_VERTICAL-2
IMD-: IMD-; NANO-FIT_VERTICAL-2
IMD-OK: YELLOW; LED-603
IMD_OK:D1: TS4148 RYG; 0805_D
IMD_OK:R1: 12K; 0603-RES
IMD_OK:R2: 43K; 0603-RES
INDICATOR: INDICATOR; NANO-FIT_VERTICAL-2
INTERLOCK1: HVP INTERLOCK; NANO-FIT_VERTICAL-2
INTERLOCK2: HVD INTERLOCK; NANO-FIT_VERTICAL-2
ISOSPI: BMS; NANO-FIT_VERTICAL-2
MAIN: MAIN; NANO-FIT_VERTICAL-10
ON-LED: BLUE; LED-603
Q1: DMG3406L; SOT23
Q2: AOD1N60; TO-252
R1, R2, R25: 10K; 0603-RES
R3, R5, R6: 510k; 0603-RES
R4: 100; 0603-RES
R7, R8, R9: 43k; 0603-RES
R10, R12, R14, R30, R31, R40: 1k; 0603-RES
R11, R13, R39, R42: 2k; 0603-RES
R15: 1.4k; 0603-RES
R16, R17, R18, R22, R26, R27, R33, R36: 10k; 0603-RES
R19, R21: 60; 0603-RES
R20, R28, R29: 1K; 0603-RES
R23, R24: 1.6K; 0603-RES
R32, R37: 10; 0603-RES
R34: 360; 0603-RES
R35: 4.7k; 0603-RES
R38: 20k; 0603-RES
R41: 8.2k; 0603-RES
RELAY: RELAY; NANO-FIT_VERTICAL-2
SHUTDOWN_H:D1: TS4148 RYG; 0805_D
SHUTDOWN_H:R1: 12K; 0603-RES
SHUTDOWN_H:R2: 43K; 0603-RES
SHUTDOWN_I:D1: TS4148 RYG; 0805_D
SHUTDOWN_I:R1: 12K; 0603-RES
SHUTDOWN_I:R2: 43K; 0603-RES
SHUTDOWN_J:D1: TS4148 RYG; 0805_D
SHUTDOWN_J:R1: 12K; 0603-RES
SHUTDOWN_J:R2: 43K; 0603-RES
SHUTDOWN_K:D1: TS4148 RYG; 0805_D
SHUTDOWN_K:R1: 12K; 0603-RES
SHUTDOWN_K:R2: 43K; 0603-RES
SOFTWARE_SHUTDOWN: SOFTWARE SHUTDOWN; G5LE-1A4
TEENSY: RED; LED-603
TEENSY3.1: TEENSY_3.2_SIMPLE
U1: HM2102NLT
U2: OPA172; SOT323-5
U3: OKI-78SR-5; OKI-78SR
U4: LTC6820; MSOP-16
U5: MCP3204; SO14
U6: STWD100PYW83F; SOT323-5
U7: SN74LVC1G08; SOT323-5
U8: CDSOT23-T24CAN-Q; SOT23
U9: TXB0104TSSOP; TSSOP-14
U10: MCP2551; SOIC-08
U11, U12, U14, U15: CPC1002N; SOP04
U13, U16: LR8; SOT89
U$3, U$4, U$5, U$6, U$7, U$8, U$9, U$10, U$11, U$13, U$14: TEST_POINTMICRO_MINIATURE; MICRO_MINIATURE
U$15, U$16, U$17: M3_MOUNTING

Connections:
60V-THRESHOLD:INPUT_POST_DIODE: 60V-THRESHOLD:D1.C, 60V-THRESHOLD:R1.1
60V_THRESHOLD_SIGNAL: 60V-THRESHOLD:D1.A, MAIN.P$1, U15.3, U$8.P$1
60V_THRESHOLD_TEENSY: 60V-THRESHOLD:R1.2, 60V-THRESHOLD:R2.1, TEENSY3.1.A6
100A_REF: 100A_REF:U1.2, CURRENT1.P$3
100A_REF:CLK: 100A_REF:C1.1, 100A_REF:U1.8
100A_REF:COM: 100A_REF:C3.1, 100A_REF:U1.1, 100A_REF:U1.6
100A_REF_FILT: 100A_REF:U1.5, U5.4
100A_SENSE: 100A_SENSE:U1.2, CURRENT1.P$2, R1.1, U2.3
100A_SENSE:CLK: 100A_SENSE:C1.1, 100A_SENSE:U1.8
100A_SENSE:COM: 100A_SENSE:C3.1, 100A_SENSE:U1.1, 100A_SENSE:U1.6
100A_SENSE_FILT: 100A_SENSE:U1.5, U5.3
300A_REF: 300A_REF:U1.2, CURRENT2.P$3
300A_REF:CLK: 300A_REF:C1.1, 300A_REF:U1.8
300A_REF:COM: 300A_REF:C3.1, 300A_REF:U1.1, 300A_REF:U1.6
300A_REF_FILT: 300A_REF:U1.5, U5.2
300A_SENSE: 300A_SENSE:U1.2, CURRENT2.P$2, R2.1
300A_SENSE:CLK: 300A_SENSE:C1.1, 300A_SENSE:U1.8
300A_SENSE:COM: 300A_SENSE:C3.1, 300A_SENSE:U1.1, 300A_SENSE:U1.6
300A_SENSE_FILT: 300A_SENSE:U1.5, U5.1
+3V3: C10.1, R11.1, R13.1, R36.1, TEENSY3.1.3.3V, U4.6, U6.5, U7.5, U9.1, U9.8, U$7.P$1
+5V: 100A_REF:C2.1, 100A_REF:U1.4, 100A_REF:U1.7, 100A_SENSE:C2.1, 100A_SENSE:U1.4, 100A_SENSE:U1.7, 300A_REF:C2.1, 300A_REF:U1.4, 300A_REF:U1.7, 300A_SENSE:C2.1, 300A_SENSE:U1.4, 300A_SENSE:U1.7, C5.1, C6.1, C7.1, C11.2, C12.2, C13.1, CURRENT1.P$1, CURRENT2.P$1, ON-LED.A, TEENSY3.1.VIN, U3.3, U4.1, U4.7, U4.8, U4.9, U4.12, U5.13, U5.14, U9.14, U10.3, U15.4, U$4.P$1
+12V: BOARDFUSE.R1, BOARDFUSE.R2, C2.2, C14.1, D3.C, ENERGYMETER.P$1, IMD.P$1, SOFTWARE_SHUTDOWN.2, U2.5, U3.1, U11.4, U12.4, U$5.P$1
+12VIN: BOARDFUSE.L1, BOARDFUSE.L2, D5.P$2, MAIN.P$4
BMS_OK: C9.2, MAIN.P$7, R16.1, R24.2, U$14.P$1
BMS_OK_3.3V: BMS-OK.A, R26.2, R34.1, U7.4, U$10.P$1
BMS_OK_PRE_FILTER: R24.1, U11.3
BMS_STATUS: D4.3, R27.2, R32.2, R33.1, TEENSY3.1.D5, U7.1
BSPD_CURR:INPUT_POST_DIODE: BSPD_CURR:D1.C, BSPD_CURR:R1.1
BSPD_CURRENT: BSPD_CURR:D1.A, MAIN.P$3, R15.2, U2.1, U$6.P$1
BSPD_CURR_TEENSY: BSPD_CURR:R1.2, BSPD_CURR:R2.1, TEENSY3.1.A7
CANH: ENERGYMETER.P$4, MAIN.P$10, R21.2, U8.2, U10.7
CANL: ENERGYMETER.P$3, MAIN.P$9, R19.2, U8.1, U10.6
CANRX: TEENSY3.1.D4(CANRX), U10.4
CANTX: TEENSY3.1.D3(CANTX), U10.1
CHARGE_ENABLE: CHARGE_ENABLE:D1.A, D2.C, MAIN.P$2
CHARGE_ENABLE:INPUT_POST_DIODE: CHARGE_ENABLE:D1.C, CHARGE_ENABLE:R1.1
CHARGE_ENABLE_TEENSY: CHARGE_ENABLE:R1.2, CHARGE_ENABLE:R2.1, TEENSY3.1.A4
CS_ADC_5V: U5.8, U9.13
CS_ADC_TEENSY: TEENSY3.1.D9(RX2), U9.2
CS_LTC6820: TEENSY3.1.D10(TX2), U4.5
DISCHARGE+: $$U$12.CONTACT2, DISCHARGE+.P$1, DISCHARGE+.P$2
GND: 60V-THRESHOLD:R2.2, 100A_REF:C1.2, 100A_REF:C2.2, 100A_REF:C3.2, 100A_REF:U1.3, 100A_SENSE:C1.2, 100A_SENSE:C2.2, 100A_SENSE:C3.2, 100A_SENSE:U1.3, 300A_REF:C1.2, 300A_REF:C2.2, 300A_REF:C3.2, 300A_REF:U1.3, 300A_SENSE:C1.2, 300A_SENSE:C2.2, 300A_SENSE:C3.2, 300A_SENSE:U1.3, $$U$12.COIL+, BSPD_CURR:R2.2, C2.1, C3.2, C4.1, C5.2, C6.2, C7.2, C8.1, C9.1, C10.2, C11.1, C12.1, C13.2, C14.2, CHARGE_ENABLE:R2.2, CURRENT1.P$4, CURRENT2.P$4, D1.A, D4.1, D5.P$1, ENERGYMETER.P$2, IMD.P$2, IMD.P$3, IMD.P$4, IMD_OK:R2.2, MAIN.P$5, Q1.2, R1.2, R2.2, R10.2, R14.2, R16.2, R17.1, R18.2, R20.2, R22.2, R25.2, R26.1, R27.1, R28.2, R29.2, R30.1, R31.2, R33.2, R36.2, RELAY.P$2, SHUTDOWN_H:R2.2, SHUTDOWN_I:R2.2, SHUTDOWN_J:R2.2, SHUTDOWN_K:R2.2, TEENSY3.1.AGND, TEENSY3.1.GND, U2.2, U3.2, U4.13, U4.14, U5.7, U5.12, U6.2, U6.3, U7.3, U8.3, U9.7, U10.2, U11.2, U12.2, U$3.P$1
HV+FUSED: HV+FUSED.P$1, HV+FUSED.P$2, IMD+.P$1, IMD+.P$2, R3.2, U13.1, U16.1
HV+UNFUSED: $$U$12.CONTACT1, C1.P$1, HV+UNFUSED.P$1, HV+UNFUSED.P$2
HV-FUSED: HV-FUSED.P$1, HV-FUSED.P$2, IMD-.P$1, IMD-.P$2, INDICATOR.P$2, Q2.3, R9.1, R38.2, R41.2
HV-UNFUSED: C1.P$2, DISCHARGE-.P$1, DISCHARGE-.P$2, HV-UNFUSED.P$1, HV-UNFUSED.P$2
IM: U1.P$10, U4.10
IMD_OK: C8.2, IMD_OK:D1.A, MAIN.P$8, R18.1, R23.2, U$13.P$1
IMD_OK:INPUT_POST_DIODE: IMD_OK:D1.C, IMD_OK:R1.1
IMD_OK_12V: IMD.P$5, IMD-OK.A, R22.1, R35.1, U$11.P$1
IMD_OK_PRE_FILTER: R23.1, U12.3
IMD_OK_TEENSY: IMD_OK:R1.2, IMD_OK:R2.1, TEENSY3.1.A5
IP: U1.P$12, U4.11
ISOSPI-M: ISOSPI.P$2, R4.2, U1.P$3
ISOSPI-P: ISOSPI.P$1, R4.1, U1.P$1
MISO_5V: U5.10, U9.11
MISO_TEENSY: R13.2, TEENSY3.1.D12, U4.3, U9.4
MOSI_5V: U5.9, U9.12
MOSI_TEENSY: R11.2, TEENSY3.1.D11, U4.2, U9.3
unnamed: D3.A, Q1.3, SOFTWARE_SHUTDOWN.1
unnamed: ON-LED.C, R20.1
unnamed: Q2.1, R37.2
unnamed: R39.2, U13.2, U13.PAD, U14.4
unnamed: R38.1, R39.1, U13.3
unnamed: R10.1, R15.1, U2.4
unnamed: R35.2, U12.1
unnamed: IMD-OK.C, R28.1
unnamed: C4.2, R19.1, R21.1
unnamed: Q1.1, R32.1
unnamed: R34.2, U11.1
unnamed: BMS-OK.C, R29.1
unnamed: R42.2, U15.1, U16.2, U16.PAD
unnamed: R3.1, R5.1
unnamed: R5.2, R6.2
unnamed: R30.2, U10.8
unnamed: R7.1, R8.1
unnamed: R8.2, R9.2
unnamed: R31.1, TEENSY.C
unnamed: R40.1, U14.2
unnamed: R12.1, U4.16
unnamed: R12.2, R14.1, U4.15
unnamed: U14.1, U15.2
unnamed: INDICATOR.P$1, U14.3
unnamed: C3.1, U1.P$11
unnamed: R41.1, R42.1, U16.3
unnamed: R6.1, R7.2, R37.1
unnamed: Q2.2(TAB), R40.2
SCK_5V: U5.11, U9.10
SCK_TEENSY: TEENSY3.1.D13, U4.4, U9.5
SHUTDOWN_H: MAIN.P$6, SHUTDOWN_H:D1.A, SOFTWARE_SHUTDOWN.P
SHUTDOWN_H:INPUT_POST_DIODE: SHUTDOWN_H:D1.C, SHUTDOWN_H:R1.1
SHUTDOWN_H_TEENSY: SHUTDOWN_H:R1.2, SHUTDOWN_H:R2.1, TEENSY3.1.A3
SHUTDOWN_I: INTERLOCK1.P$1, SHUTDOWN_I:D1.A, SOFTWARE_SHUTDOWN.S
SHUTDOWN_I:INPUT_POST_DIODE: SHUTDOWN_I:D1.C, SHUTDOWN_I:R1.1
SHUTDOWN_I_TEENSY: SHUTDOWN_I:R1.2, SHUTDOWN_I:R2.1, TEENSY3.1.A2
SHUTDOWN_J: INTERLOCK1.P$2, INTERLOCK2.P$1, SHUTDOWN_J:D1.A
SHUTDOWN_J:INPUT_POST_DIODE: SHUTDOWN_J:D1.C, SHUTDOWN_J:R1.1
SHUTDOWN_J_TEENSY: SHUTDOWN_J:R1.2, SHUTDOWN_J:R2.1, TEENSY3.1.A1
SHUTDOWN_K: $$U$12.COIL-, D1.C, D2.A, INTERLOCK2.P$2, RELAY.P$1, SHUTDOWN_K:D1.A
SHUTDOWN_K:INPUT_POST_DIODE: SHUTDOWN_K:D1.C, SHUTDOWN_K:R1.1
SHUTDOWN_K_TEENSY: SHUTDOWN_K:R1.2, SHUTDOWN_K:R2.1, TEENSY3.1.A0
TEENSY_STATUS: TEENSY.A, TEENSY3.1.D6
WATCHDOG_INPUT: R25.1, TEENSY3.1.D7(RX3), U6.4
WATCHDOG_OK: R17.2, U6.1, U7.2, U$9.P$1

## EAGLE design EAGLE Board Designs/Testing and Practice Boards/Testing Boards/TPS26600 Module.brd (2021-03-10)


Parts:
C1, C2, C3: CAP0603-CAP; 0603-CAP
JP1: M04_SLIM; 1X04_SLIM
R1, R2, R3, R4, R5: RESISTOR0603; 0603-RES
U$1: TPS26600; HTSSOP-16

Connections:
GND: C1.1, C2.1, JP1.3, U$1.9 (GND)
IMON: JP1.1, R4.2, U$1.10 (IMON)
IN: C1.2, JP1.4, R1.2, U$1.1 (IN), U$1.2 (IN)
unnamed: R1.1, R2.2, U$1.3 (UVLO)
unnamed: R2.1, R3.2, U$1.5 (OVP)
unnamed: C3.2, U$1.12 (DVDT)
unnamed: R5.2, U$1.11 (ILIM)
unnamed: C3.1, R3.1, R4.1, R5.1, U$1.6 (MODE), U$1.8 (RTN), U$1.PAD (RTN)
OUT: C2.2, JP1.2, U$1.15 (OUT), U$1.16 (OUT)



Board: 2 copper layers, 12.2 x 11.0 mm, 10 parts (6 on the bottom side), 9 nets.

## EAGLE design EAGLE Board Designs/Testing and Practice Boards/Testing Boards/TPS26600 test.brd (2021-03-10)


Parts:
PO-1, PO-2: M06; 1X06
U1: TPS26600; HTSSOP-16

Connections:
DVDT: PO-2.3, U1.12 (DVDT)
FLT: PO-2.2, U1.14 (FLT)
GND: PO-2.6, U1.9 (GND)
ILIM: PO-2.4, U1.11 (ILIM)
IMON: PO-2.5, U1.10 (IMON)
IN: PO-1.6, U1.1 (IN), U1.2 (IN)
MODE: PO-1.3, U1.6 (MODE)
OUT: PO-2.1, U1.15 (OUT), U1.16 (OUT)
OVP: PO-1.4, U1.5 (OVP)
RTN: PO-1.1, U1.8 (RTN), U1.PAD (RTN)
SHDN: PO-1.2, U1.7 (SHDN)
UVLO: PO-1.5, U1.3 (UVLO)


Board: 1 copper layer, 20.0 x 19.0 mm, 3 parts (1 on the bottom side), 12 nets.

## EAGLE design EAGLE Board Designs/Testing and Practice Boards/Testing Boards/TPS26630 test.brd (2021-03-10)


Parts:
JP1, JP2: M08; 1X08
TPS26630-1: TPS26630; HTSSOP-20

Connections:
B_GATE: JP1.7, TPS26630-1.4 (B_GATE)
DRV: JP1.6, TPS26630-1.5 (DRV)
DVDT: JP1.1, TPS26630-1.10 (DVDT)
FLT: JP2.4, TPS26630-1.15 (FLT)
GND: JP1.2, TPS26630-1.9 (GND), TPS26630-1.PAD (GND)
ILIM: JP2.8, TPS26630-1.11 (ILIM)
IMON: JP2.5, TPS26630-1.14 (IMON)
IN: JP1.8, TPS26630-1.1 (IN), TPS26630-1.2 (IN), TPS26630-1.3 (IN)
IN_SYS: JP1.5, TPS26630-1.6 (IN_SYS)
MODE: JP2.7, TPS26630-1.12 (MODE)
OUT: JP2.1, TPS26630-1.18 (OUT), TPS26630-1.19 (OUT), TPS26630-1.20 (OUT)
OVP: JP1.3, TPS26630-1.8 (OVP)
PGOOD: JP2.2, TPS26630-1.17 (PGOOD)
PGTH: JP2.3, TPS26630-1.16 (PGTH)
SHDN: JP2.6, TPS26630-1.13 (SHDN)
UVLO: JP1.4, TPS26630-1.7 (UVLO)


Board: 1 copper layer, 23.0 x 22.9 mm, 3 parts (1 on the bottom side), 16 nets.

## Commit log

2019-08-25 Removed old harness and external diagrams
    Removed old ECUs
    Removed more old files
    Removed old Main ECU and HV Boards versions
    Removed BMS boards
    [0805 Breakout Board.brd, 0805 Breakout Board.sch, 555 Oscillator Board.brd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]
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2019-09-18 Added resistor values for the BSPD timing circuit.
    Changed resistor from 330 -> 8200, added values on voltage divider (220, 330).
    [MainECU rev8.brd, MainECU rev8.sch]
2019-09-20 Verified that AND gate with drain and comparator function properly.
    Note: resistor and capacitor values are subject to change; 100ms at present.
    [MainECU rev8.brd, MainECU rev8.sch]
2019-09-20 Fixed board width to be solvable
    [ADIS16209_Teensy.brd, ADIS16209_Teensy.sch]
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2019-09-26 updated the rev2 to switch to 3.3V supply and changed the layout so the dude at electronics lab will not be mad at Yvonne
    [ADIS16209 Teensy rev2.brd, ADIS16209 Teensy rev2.sch]
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2019-10-11 added broadcom current sensor to the library. schematic cleanup. started on the layout
    [MainECU rev9.brd, MainECU rev9.sch]
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2019-10-21 changed caps and resistors to 0603 package and WIP on the layout
    [MainECU rev9.brd, MainECU rev9.sch]
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2019-10-28 Replaced all parts with 0603 eqivalents and expanded springs to 11 mm's size
    [BMS Board Outline.brd, BMS Segment rev10.dxf, BMS Segment rev11.brd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]
2019-10-28 Fixed minor issues
    [BMS Segment rev11.brd]
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2019-11-01 Fixed LTC6081 device
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2019-11-01 Swapped in LTC6811 Part and added attributes
    [BMS Segment rev11.brd, BMS Segment rev11.sch]
2019-11-01 Replaced 6804 references with 6811
    [BMS Segment rev11.brd, BMS Segment rev11.sch]
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2019-11-03 0 DRC errors goddammit
    [MainECU rev9.brd, MainECU rev9.sch]
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2019-11-11 Fixed pull-down transistors on gate
    [Tractive System Active Light rev1.brd, Tractive System Active Light rev1.sch]
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2019-11-13 Added wheel speed sensor board with SMD components and DRC for use with the Hive's PCB fabrication equipment
    [Wheel Speed Sensor smd.brd, Wheel Speed Sensor smd.sch]
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2019-11-15 Revised TSAL Design
    Names, values, and logos repositioned.
    Top edge of board changed to a curve.
    [Tractive System Active Light rev1.brd, Tractive System Active Light rev1.sch]
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2019-11-18 removed AGND connection from the Teensy 3.2 and 3.5 and fixed names on the board
    [MainECU rev9.brd, MainECU rev9.sch]
2019-11-19 Fixed clearance issues
    [ADIS16209_v3.brd, ADIS16209_v3.sch]
2019-11-20 Increment Changes made to routing
    - Pending issue: duplicate naming of BMS_OK signal in the schematic view, need schematic re-do and re-spin the layout because of the fact.
    [Charger Control Board rev3.brd, Charger Control Board rev3.sch]
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2019-12-01 Fixed TSAL to be correct version from git history
    [Tractive System Active Light rev1.brd, Tractive System Active Light rev1.sch]
2019-12-01 Fixed library for LED part
2019-12-01 Fixed schematic/board to have new fixed part
    [Tractive System Active Light rev1.brd, Tractive System Active Light rev1.sch]
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2019-12-02 Renamed TSAL to be correct spelling
    [Tractive System Active Light rev1.brd, Tractive System Active Light rev1.sch]
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2019-12-04 Added two new text circuits
    Added two new test circuits to the board in line with a circuit described in a document published by TI for strain gauge amplification
    [SGWB circuit test board rev1.brd, SGWB circuit test board rev1.sch]
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2019-12-07 Cleared DRC Errors
    As titled
    [Charger Control Board rev3.brd]
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2019-12-08 Cleaned up some ERC and DRC errors/warnings
    Approved supply ERC errors, cleaned up wire stub DRC errors
    [MainECU rev9.brd, MainECU rev9.sch]
2019-12-09 Approved ERC and DRC errors, schematic style
    [BMS Segment rev11.brd, BMS Segment rev11.sch]
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2019-12-09 Revert_to_previous_version
    revert
    [Charger Control Board rev3.brd]
2019-12-09 Revert "Shutdown_D->Charge_Enable Change"
    This reverts commit 13512f0f830e8f5d48520765668ed1b52794a502.
    [Charger Control Board rev3.brd, Charger Control Board rev3.sch]
2019-12-09 Revert "Revert "Shutdown_D->Charge_Enable Change""
    This reverts commit 5561f356f6bb76e18dd198f7535da16a58f27f9d.
    [Charger Control Board rev3.brd, Charger Control Board rev3.sch]
2019-12-09 Fixed board file, can load board now
    [Charger Control Board rev3.brd]
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2019-12-09 Approved 3 DRC errors
    [BMS Segment rev11.brd]
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2019-12-10 Fixed thermal pads to have seperate net
    [Tractive System Active Light rev1.brd, Tractive System Active Light rev1.sch]
2019-12-10 Made small adjustments and fixed multiple GNDs
    [Charger Control Board rev3.brd]
2019-12-11 Fixed board widths
    [Charger Control Board rev3.brd, Charger Control Board rev3.sch]
2019-12-11 Fixed silkscreen
    [Charger Control Board rev3.brd]
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2019-12-12 Fixed other 2
    [BMS Cell Charging Adapter rev1.brd]
2019-12-13 ERC fixes
    [Charger Control Board rev3.sch]
2019-12-14 Fixed ADIS practice board name and adjusted silkscreen
    [ADIS16209 Soldering Practice.brd]
2019-12-14 Fixed measurement on wrong layer
    [BMS Cell Charging Adapter rev1.brd]
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2019-12-16 Added inital panel layout for the HV Board, Charger Controller, Strain guage, TSAL, and ADIS practice board
    [Charger Controller, HV Board, TSAL, Strain Guage, and ADIS Practice.brd]
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2019-12-20 Adjusted voltage sources to op-amps
    Changed op-amps in TI based circuits to 5V and added a disconnect for non-TI circuits to enable 5V power through jumper wire.
    Added single header pins to measure intermediate amplification voltages on all four circuits and the baseline voltage for TI based circuits
    [SGWB circuit test board rev1.brd, SGWB circuit test board rev1.sch]
2019-12-20 Changed voltage divider resistors
    Changed 1k resistors to 86.6 ohm resistor to increase current flow
    [SGWB circuit test board rev1.brd, SGWB circuit test board rev1.sch]
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2020-01-05 Updated tolerances
    [BMS Segment rev11.brd, BMS Segment rev11.sch]
2020-01-10 Adjusted tolerances to 1% for resistors and 5% for caps
    [BMS Segment rev11.brd, BMS Segment rev11.sch]
2020-01-12 Added tolerances and voltage ratings
    [Tractive System Active Light rev1.brd, Tractive System Active Light rev1.sch]
2020-01-12 Fixed 1% to 5% tolerance
    [BMS Segment rev11.brd, BMS Segment rev11.sch]
2020-01-13 Updated 100V tolerance to 50V for caps
    [BMS Segment rev11.brd, BMS Segment rev11.sch]
2020-01-17 Fixed holes on TSAL
    [Tractive System Active Light rev1.brd]
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2020-02-05 Removed unnecessary resistor, adjusted brightness controlling resistor, and adjusted flashing frequency to 3.529 hertz
    [Tractive System Active Light rev2.brd, Tractive System Active Light rev2.sch]
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2020-02-16 Fixed reverse conventions on power and ground
    [Tractive System Active Light rev2.brd, Tractive System Active Light rev2.sch]
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2020-02-21 Updated board outline to show bottom pads and adjusted layers/measures on B;5DMS rev12
    [BMS Board Outline.brd, BMS Segment rev12.brd, BMS Segment rev12.sch]
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2020-02-23 Started updating layout schematic and made it more clear what the board outline is of
    [BMS Layout rev6.sch, BMS Segment rev12 Board Outline.brd]
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2020-02-24 Began work on rev2, reduced size of therrmal pads, added pull down, and removed old silkscreen
    [Tractive System Active Light rev2.brd, Tractive System Active Light rev2.sch]
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2020-02-25 Adjusted board boundaries to better fit chassis tube and adjusted mounting hole locations
    [Tractive System Active Light rev2.brd]
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2020-02-26 Finalized mounting holes for TSAL and LED locations, plus adjusted heatsinking pads
    [Tractive System Active Light rev2.brd, Tractive System Active Light rev2.sch]
2020-02-27 Finalized routing of board, need to fix silkscreen
    [Tractive System Active Light rev2.brd]
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2020-03-02 Fixed via on top of capacitor silkscreen
    [Tractive System Active Light rev2.brd]
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2020-03-03 Fixed vias to be tented and moved some silkscreen/traces
    [Tractive System Active Light rev2.brd]
2020-03-03 Ran DRC/ERC and checked off everything on the board was good except logos
    [Tractive System Active Light rev2.brd, Tractive System Active Light rev2.sch]
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2020-03-04 Revert "Changed to use RT424009 for all shutdown circuit"
    This reverts commit 623f8aa93397a8ee771612fbc13354bca33b6a52.
    [Charger Control Board rev4.brd, Charger Control Board rev4.sch]
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2020-03-04 Flipped relay coil direction
    [Charger Control Board rev4.brd, Charger Control Board rev4.sch]
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2020-03-06 Added zeners to protect mosfet gates and adjusted logo to be on copper for best after-dark result
    [Tractive System Active Light rev2.brd, Tractive System Active Light rev2.sch]
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2020-03-06 fix bottom layer silkscreen
    [Charger Control Board rev4.brd]
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2020-03-06 Adjustd silkscreen slightly on top, fixed trace width for 5V power, and approved oshpark DRC dimension issues
    [Charger Control Board rev4.brd]
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2020-03-06 Fixed Teensy 3.5 name, overlapping traces, align can term jumper
    [Charger Control Board rev4.brd, Charger Control Board rev4.sch]
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2020-03-06 Fixed random airwire after DRC issue
    [Charger Control Board rev4.brd]
2020-03-06 Approved width DRC errors from logos
    [Tractive System Active Light rev2.brd]
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2020-03-06 Approve DRC width errors, fixed DRC warnings
    [keychain_rev2.brd]
2020-03-06 Fix silkscreen
    [keychain_rev2.brd]
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2020-03-07 Moved logos to docu layers and made dimensions clearer to show LED location reasoning
    [Tractive System Active Light rev2.brd]
2020-03-07 Fixed offset traces and silkscreen
    [Charger Control Board rev4.brd, Charger Control Board rev4.sch]
2020-03-10 Created rev 5 with silkscreen fix not able to be caught before rev 4 was sent out
    [Charger Control Board rev5.brd, Charger Control Board rev5.sch]
2020-03-10 Replaced holes with mounting parts and updated LTC part
    [BMS Segment rev12.brd, BMS Segment rev12.sch]
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2020-03-10 Fixed dimension of silkscreen around fuses
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2020-03-11 Fixing silkscreen
    [BMS Segment rev12.brd, BMS Segment rev12.sch]
2020-03-11 Fixed small routing issues
    [BMS Segment rev12.brd]
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2020-03-12 Fixed silkscreen for readability
    [BMS Segment rev12.brd]
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2020-03-12 Fixed TS/isoSPI silkscreen direction
    [BMS Segment rev12.brd]
2020-03-12 Fixed values to make BOM easier to read
    [Tractive System Active Light rev2.brd, Tractive System Active Light rev2.sch]
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2020-06-21 Fixed JLC through-hole drc error
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2020-06-25 Adjusted Panelized Orders to have Eagle files used at the time of the order
    [ADIS16209 Practice Board.brd, Charger Control Board rev3.brd, Dashboard rev1.brd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]
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2020-07-04 More silkscreen fixes
    [BMS Segment rev12.brd]
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2020-07-05 Adjusted a missed LTC6804 reference to LTC6811
    [BMS Segment rev12.sch]
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2020-07-06 Dashboard rev1 (#49)
    * added dashboard schematic and board files
    * removed pictures and pdfs
    [Dashboard rev1.brd, Dashboard rev1.sch]
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2020-07-19 HV Board rev 12 (#52)
    * Work in progress
    * Adjusted library
    * Continued routing
    * Fixing eagle part
    * Adjusted filter positions
    * Fixed library part for isolated gate driver
    * Continuing work
    * Continuing routing
    * Finished routing
    * Adjusting schematic slightly
    * Removed unnecessary capacitors and added sense for 60V threshold
    * Removed all values
    * Working on silkscreen
    * Added sensing for OKHS
    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
    [HV Board rev12.brd, HV Board rev12.sch]
2020-10-20 BMS rev 13/14 (#55)
    * Added rev 13 initial swapover
    * Used rev 12 updated to share locations of resistors
    * Fixed overlapping traces
    * Added rev 13 mechancial outline
    * Improved rev 6 BMS layout
    * Removed rev13 outline
    * Created rev 13 and rev 14 that will be modified with the HT05 spring layout
    * Fixed incorrect datasheet references
    * Updated routing with rev12 fixes
    * Updated both schematics and boards to latest library
    * Added HVD to diagram
    * Added energy meter
    * Updated layout
    * Added frame to rev13 schematic
    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
    [BMS Layout rev6.sch, BMS Segment rev12 Mechanical Outline.brd, BMS Segment rev13 Mechanical Outline.brd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]
2020-10-25 Dashboard rev2 (#56)
    * Dashboard rev2
    Space out LEDs
    Updated resistor array
    Added SSOK read
    * Made board compliant with general HyTech DRC
    * Board passes DRC
    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
    [Dashboard rev2.brd, Dashboard rev2.sch]
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2020-10-25 Enerdal adapter rev5 (#59)
    * Created the enerdel adapter rev5 files
    * Finished the enerdal adapter rev 5 of the pcb design
    * Updated the Enerdal_Adapter
    * Made file changes so that the files were correctly named
    * Corrected the dimentions layer of the board design
    * Changed the mounting holes to the M4 mounting hole device from the HyTech Library and verified the board
    * Adjusted schematic/board
    * Added frame to schematic and measures to board
    [BMS Enerdel Adapter rev4.sch, BMS Enerdel Adapter rev5.brd, BMS Enerdel Adapter rev5.sch]
2020-11-01 Ecu rev10 analog split (#60)
    * Start working rev 10
    * Started schematic changes
    Removed dashboard components
    Changed shutdown circuit to OPA990
    * Updated shutdown circuitry
    Added OR gates
    Added signal reads
    Added signal LEDs
    * Added wheel speed hardware
    * Fixed Teensy GPIO
    Moved fan control
    Added software outputs
    * TXB0106 Accuracy
    Added pull down resistor on OE per datasheet
    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
    [MainECU rev10.brd, MainECU rev10.csv, MainECU rev10.sch]
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2020-11-03 Cell Charging Adapter Rev2 (#58)
    * Created new file for the second cell charger revision
    * Create TPS26600 test.sch
    * Changed the locations of the pads on the charger controller pcb layout
    * changed the locations of the pads in the Cell Charging adapter board
    * Made changes to the charger adapter rev2 board
    * Added center mounting holes to the pcb design
    * Finished changing the dimensions of the pcb and adding center mount holes
    * Moved drill holes to the correct locations
    * Altered the dimention layer and moved a via in the board layout
    * Made sure that the cell charging adapter complied with the BMS rev 13 design
    * Changed the mounting holes to the M4 mounting hole device from th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
    [BMS Cell Charging Adapter rev1.brd, BMS Cell Charging Adapter rev2.brd, BMS Cell Charging Adapter rev2.sch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]
2020-11-13 Ecu rev10 analog split (#62)
    * Added TXB0104 and MCP3204
    * Removed AGND
    Removed AGND
    Removed current sense jumpers
    Moved fan control to PWM pin
    * Schematic complete
    Added I/O to autosport connector
    Decided not to include resistors between ADC and TXB.
    Moved software shutdown to 3.3V logic
    * Remov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
    [MainECU rev10.brd, MainECU rev10.sch]
2020-11-22 Fixed erc warnings on rev12 (#64)
    [HV Board rev12.sch]
2020-11-22 BMS Patch (#65)
    * Fixed erc warnings on rev12
    * Attempt to fix too large text on sheets
    * Adjusted slighty
    [BMS Segment rev13.sch, BMS Segment rev14.sch]
2021-03-10 E fuse (#66)
    * Created the schematic and pcb layout for the TPS26600 testing board
    * Made changes to the pcb and schematic to comply with Hytech conventions
    * Changed the pcb and schematic layouts to comply with Hytech standards
    * Updated the E-Fuse board so that it is ready for production
    * Created a schematic for the TPS26630 breakout board and began the pcb layout
    * Finished the TPS26630 E-Fuse breakout board layout
    * Made changes to the TPS26630 test board so that it is ready to be manufactured
    * Made sure the board was correct before ordering it
    * Created TPS 26600 module board
    * Made it so that there were no drc errors
    [TPS26600 Module.brd, TPS26600 Module.sch, TPS26600 test.brd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]
2021-04-06 Hv board rev 13 (#71)
    * Pull down 60V_THRESHOLD_SIGNAL
    * HV board rev 12 done
    * Changed NE Op-amp to generic
    * Added top copper pour
    * Adjusted traces slightly
    * Increased via sizes, fixed silkscreen labels, approved ERC and DRC errors
    * Fixed one via
    * Adjus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
    [BSPD_rev11_v2.brd, HV Board rev13.brd, HV Board rev13.sch]
2021-04-06 DC-DC Converter rev1 (#76)
    * created dc dc converter schematic
    * Made changes
    * Added new cap and made board
    * changed plane sizes, fixed traces
    * fixed trace widths
    * Made changes to the board layout to be the correct size
    * Deleted old libraries
    * Made more changes to dc dc converter
    * Fixed the packages
    * Fixed the packages
    * fixed git's fun with dc-dc
    * Finished dc dc board
    * Updated dc dc converter
    * Updated dc dc converter board design
    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
    [DC_DC_Converter_rev1.brd, DC_DC_Converter_rev1.sch]
2021-06-16 System diagram (#80)
    * started working on new system diagram
    * more edits to dashboard
    * updated main ecu io
    * updated system in front of firewall
    * small edits
    * TS internals updates
    * small edits
    * finishing up TS, shutdown, edits to power switching
    * finished rough draft
    * small aesthetic fixes
    * power switching small edit
    * added exported image
    * added TSAL
    * small edits
    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
    [External Diagram FSAE 2021.sch]
2021-06-16 Hv board rev 14 (#81)
    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
    [HV Board rev14.brd, HV Board rev14.sch]
2021-06-16 Esf schematics (#82)
    * added ESF schematics
    * small schematic edits
    * more small edits
    * fixed mistakes in ESF version of BSPD rev10
    * updated ESF schematics
    * exported images
    [Accumulator TS Internals.sch, BSPD rev10.sch, Battery Segment.sch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]
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
